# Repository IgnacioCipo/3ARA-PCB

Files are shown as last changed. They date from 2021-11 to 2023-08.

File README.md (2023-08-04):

# 3ARA-PCB

# Introduction
This repo holds the electronic boards of the project designed using KiCad.

# Images







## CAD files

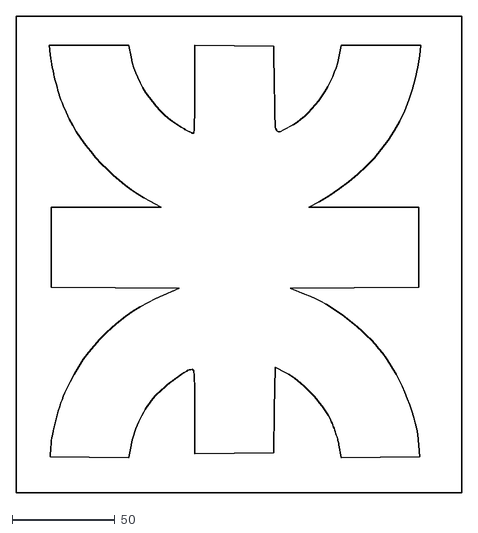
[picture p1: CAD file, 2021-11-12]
3ARA_PCB/logo_utn_kicad.dxf
217.0 x 232.0

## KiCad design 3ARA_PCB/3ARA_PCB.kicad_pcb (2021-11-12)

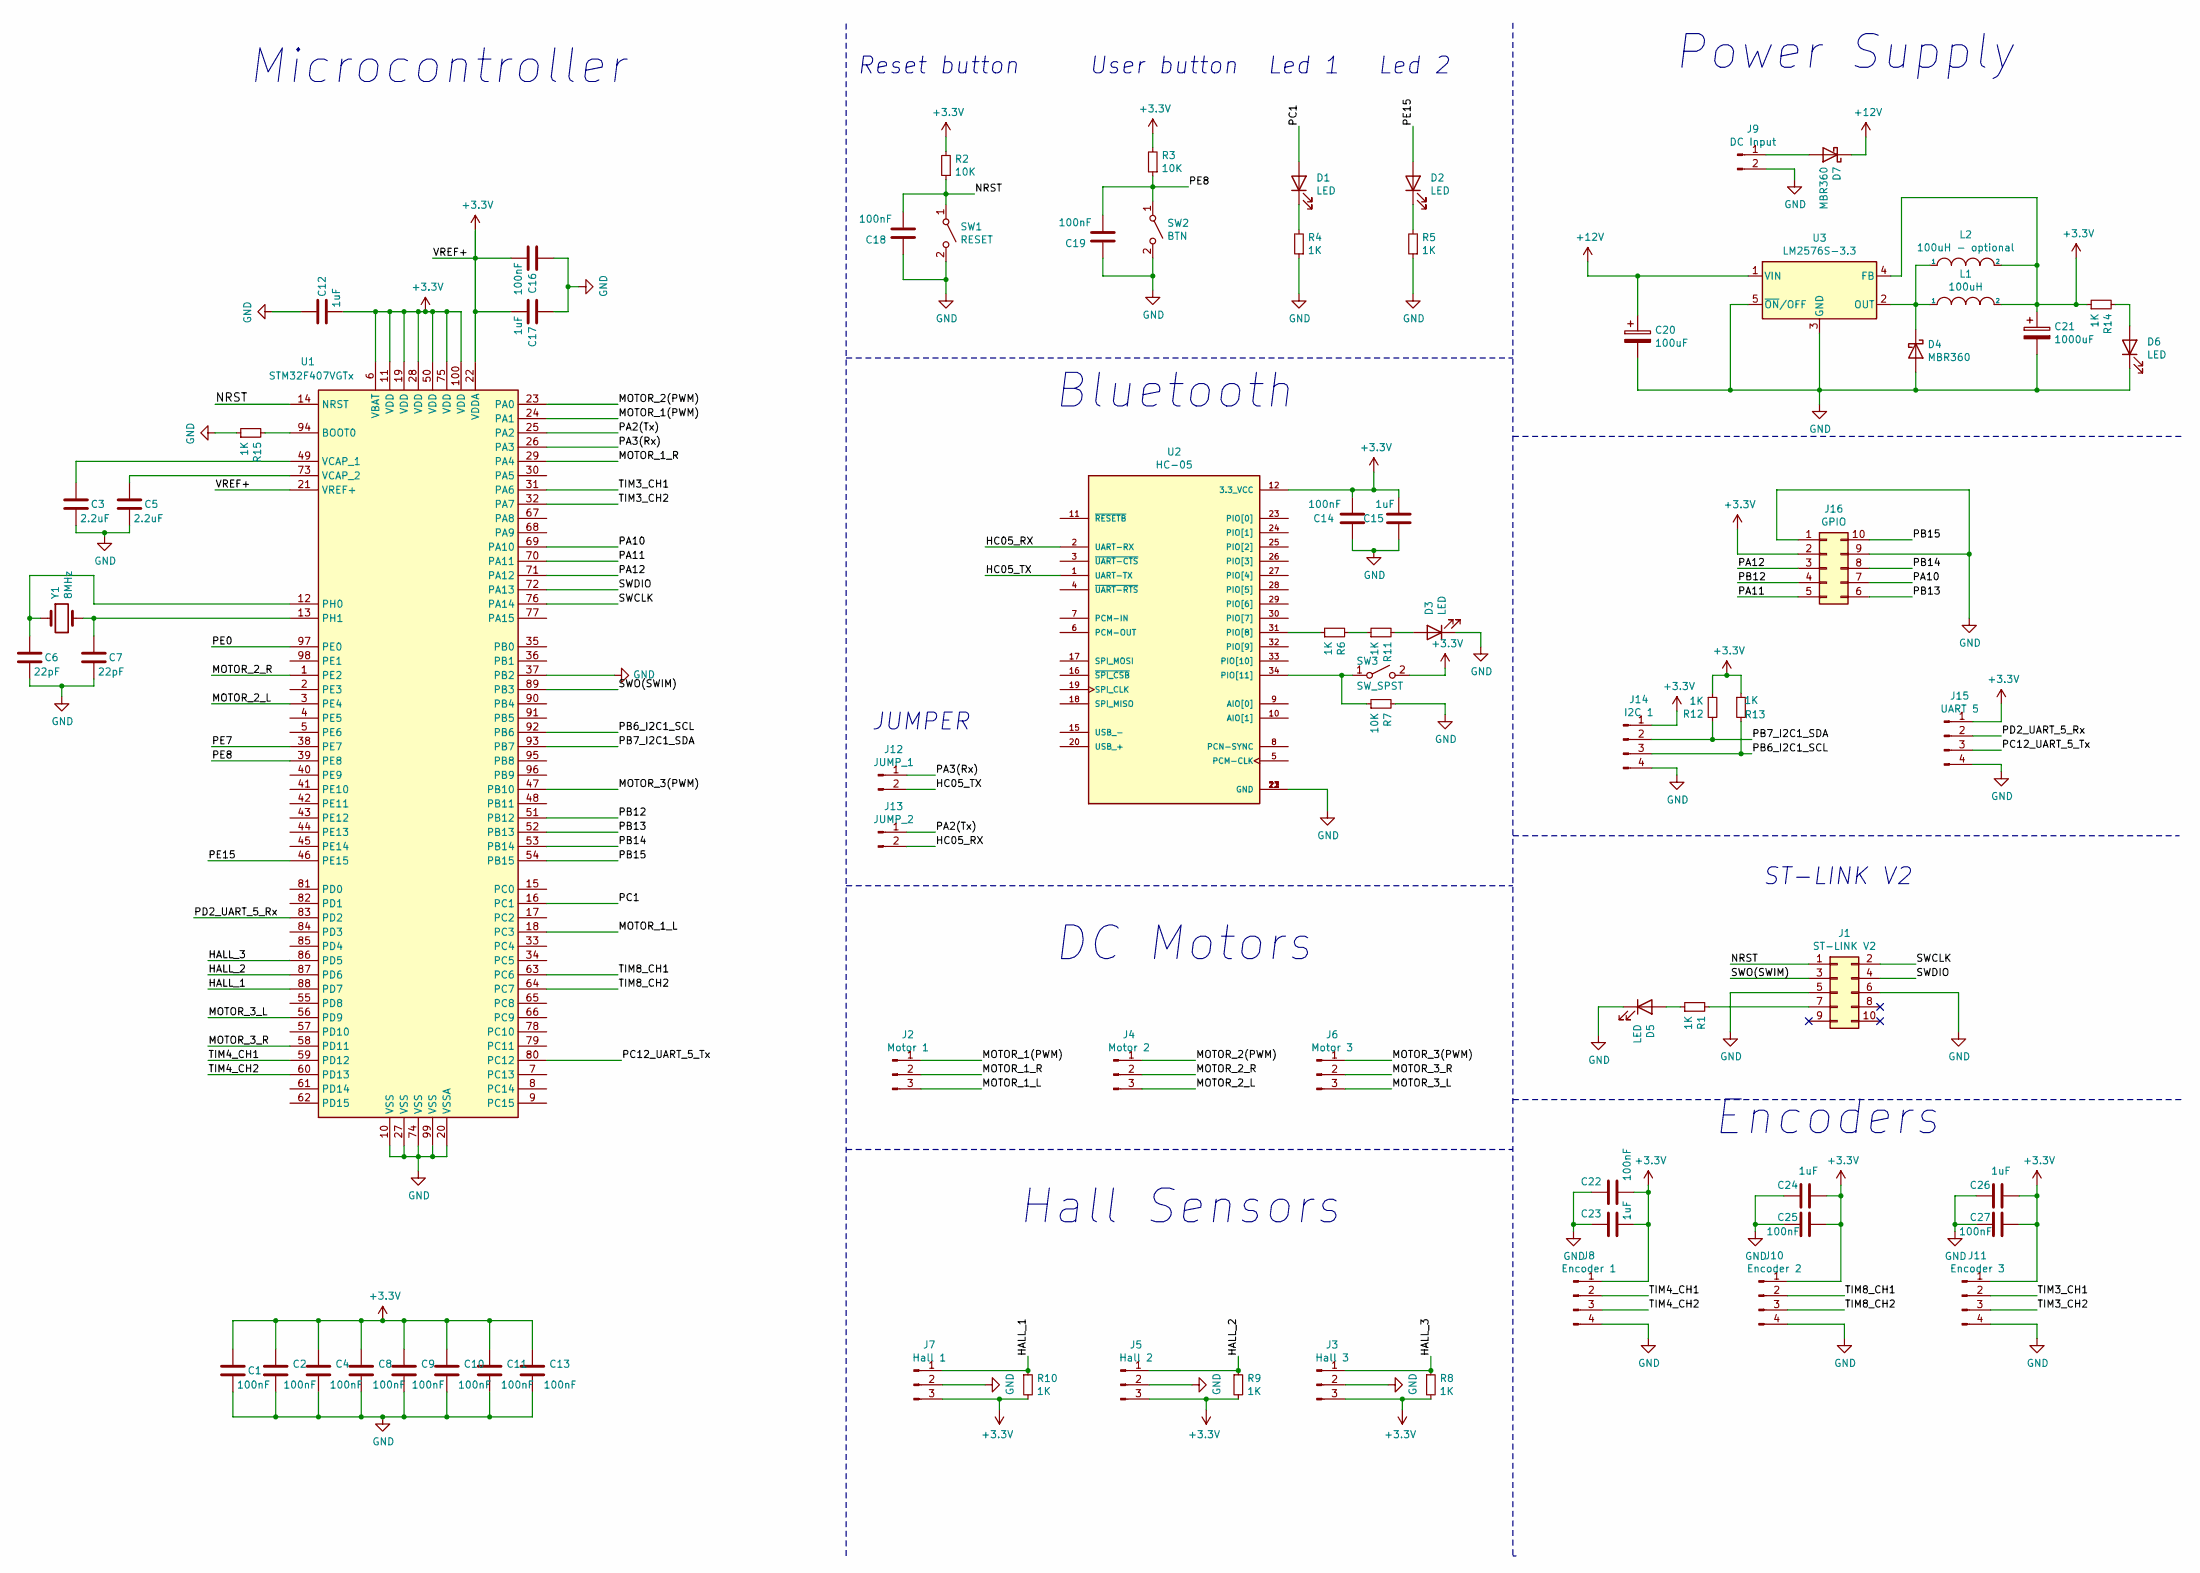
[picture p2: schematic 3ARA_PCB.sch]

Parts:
C1, C2, C4, C8, C9, C10, C11, C13, C14, C16, C18, C19, C22, C25, C27: 100nF; C_0805_2012Metric_Pad1.18x1.45mm_HandSolder
C3, C5: 2.2uF; C_Disc_D3.8mm_W2.6mm_P2.50mm
C6, C7: 22pF; C_0805_2012Metric_Pad1.18x1.45mm_HandSolder
C12, C15, C17, C23, C24, C26: 1uF; C_0805_2012Metric_Pad1.18x1.45mm_HandSolder
C20: 100uF; CP_Elec_6.3x5.4
C21: 1000uF; CP_Radial_D8.0mm_P3.50mm
D1, D6: LED; LED_1206_3216Metric_Pad1.42x1.75mm_HandSolder
D2, D3, D5: LED; LED_0805_2012Metric_Pad1.15x1.40mm_HandSolder
D4, D7: MBR360; D_SMA_Handsoldering
J1: ST-LINK V2; IDC-Header_2x05_P2.54mm_Vertical
J2: Motor 1; JST_EH_B3B-EH-A_1x03_P2.50mm_Vertical
J3: Hall 3; JST_EH_B3B-EH-A_1x03_P2.50mm_Vertical
J4: Motor 2; JST_EH_B3B-EH-A_1x03_P2.50mm_Vertical
J5: Hall 2; JST_EH_B3B-EH-A_1x03_P2.50mm_Vertical
J6: Motor 3; JST_EH_B3B-EH-A_1x03_P2.50mm_Vertical
J7: Hall 1; JST_EH_B3B-EH-A_1x03_P2.50mm_Vertical
J8: Encoder 1; JST_EH_B4B-EH-A_1x04_P2.50mm_Vertical
J9: DC Input; JST_EH_B2B-EH-A_1x02_P2.50mm_Vertical
J10: Encoder 2; JST_EH_B4B-EH-A_1x04_P2.50mm_Vertical
J11: Encoder 3; JST_EH_B4B-EH-A_1x04_P2.50mm_Vertical
J12: JUMP_1; PinHeader_1x02_P2.54mm_Vertical
J13: JUMP_2; PinHeader_1x02_P2.54mm_Vertical
J14: I2C 1; JST_EH_B4B-EH-A_1x04_P2.50mm_Vertical
J15: UART 5; JST_EH_B4B-EH-A_1x04_P2.50mm_Vertical
J16: GPIO; PinHeader_2x05_P2.54mm_Vertical
L1: 100uH; L_12x12mm_H6mm
L2: 100uH - optional; L_Axial_L9.5mm_D4.0mm_P15.24mm_Horizontal_Fastron_SMCC
R1, R4, R5, R6, R8, R9, R10, R11, R12, R13, R14, R15: 1K; R_0805_2012Metric_Pad1.20x1.40mm_HandSolder
R2, R3, R7: 10K; R_0805_2012Metric_Pad1.20x1.40mm_HandSolder
SW1: RESET; SW_PUSH_6mm
SW2: BTN; SW_PUSH_6mm
SW3: SW_SPST; SW_PUSH_6mm
U1: STM32F407VGTx; LQFP-100_14x14mm_P0.5mm
U2: HC-05; XCVR_HC-05; PARTREV v1.0
U3: LM2576S-3.3; TO-263-5_TabPin3
Y1: 8MHz; Crystal_HC49-U_Vertical

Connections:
+3V3: C1.1, C2.1, C4.1, C8.1, C9.1, C10.1, C11.1, C12.2, C13.1, C14.2, C15.2, C16.2, C17.2, C21.1, C22.2, C23.2, C24.1, C25.1, C26.1, C27.1, J3.3, J5.3, J7.3, J8.1, J10.1, J11.1, J14.1, J15.1, J16.2, L1.2, L2.2, R2.2, R3.2, R8.2, R9.2, R10.2, R12.1, R13.1, R14.1, SW3.2 (B), U1.6 (VBAT), U1.11 (VDD), U1.19 (VDD), U1.21 (VREF+), U1.22 (VDDA), U1.28 (VDD), U1.50 (VDD), U1.75 (VDD), U1.100 (VDD), U2.12 (3.3_VCC), U3.4 (FB)
+12V: C20.1, D7.1 (K), U3.1 (VIN)
/HALL_1: J7.1, R10.1, U1.88 (PD7)
/HALL_2: J5.1, R9.1, U1.87 (PD6)
/HALL_3: J3.1, R8.1, U1.86 (PD5)
/HC05_RX: J13.2, U2.2 (UART-RX)
/HC05_TX: J12.2, U2.1 (UART-TX)
/MOTOR_1(PWM): J2.1, U1.24 (PA1)
/MOTOR_1_L: J2.3, U1.18 (PC3)
/MOTOR_1_R: J2.2, U1.29 (PA4)
/MOTOR_2(PWM): J4.1, U1.23 (PA0)
/MOTOR_2_L: J4.3, U1.3 (PE4)
/MOTOR_2_R: J4.2, U1.1 (PE2)
/MOTOR_3(PWM): J6.1, U1.47 (PB10)
/MOTOR_3_L: J6.3, U1.56 (PD9)
/MOTOR_3_R: J6.2, U1.58 (PD11)
/NRST: C18.2, J1.1, R2.1, SW1.1 (A), U1.14 (NRST)
/PA2(Tx): J13.1, U1.25 (PA2)
/PA3(Rx): J12.1, U1.26 (PA3)
/PA10: J16.7, U1.69 (PA10)
/PA11: J16.5, U1.70 (PA11)
/PA12: J16.3, U1.71 (PA12)
/PB6_I2C1_SCL: J14.3, R13.2, U1.92 (PB6)
/PB7_I2C1_SDA: J14.2, R12.2, U1.93 (PB7)
/PB12: J16.4, U1.51 (PB12)
/PB13: J16.6, U1.52 (PB13)
/PB14: J16.8, U1.53 (PB14)
/PB15: J16.10, U1.54 (PB15)
/PC1: D1.2 (A), U1.16 (PC1)
/PC12_UART_5_Tx: J15.3, U1.80 (PC12)
/PD2_UART_5_Rx: J15.2, U1.83 (PD2)
/PE8: C19.2, R3.1, SW2.1 (A), U1.39 (PE8)
/PE15: D2.2 (A), U1.46 (PE15)
/SWCLK: J1.2, U1.76 (PA14)
/SWDIO: J1.4, U1.72 (PA13)
/SWO(SWIM): J1.3, U1.89 (PB3)
/TIM3_CH1: J11.2, U1.31 (PA6)
/TIM3_CH2: J11.3, U1.32 (PA7)
/TIM4_CH1: J8.2, U1.59 (PD12)
/TIM4_CH2: J8.3, U1.60 (PD13)
/TIM8_CH1: J10.2, U1.63 (PC6)
/TIM8_CH2: J10.3, U1.64 (PC7)
GND: C1.2, C2.2, C3.2, C4.2, C5.2, C6.2, C7.2, C8.2, C9.2, C10.2, C11.2, C12.1, C13.2, C14.1, C15.1, C16.1, C17.1, C18.1, C19.1, C20.2, C21.2, C22.1, C23.1, C24.2, C25.2, C26.2, C27.2, D3.1 (K), D4.2 (A), D5.1 (K), D6.1 (K), J1.5, J1.6, J3.2, J5.2, J7.2, J8.4, J9.2, J10.4, J11.4, J14.4, J15.4, J16.1, J16.9, R4.1, R5.1, R7.2, R15.1, SW1.2 (B), SW2.2 (B), U1.10 (VSS), U1.20 (VSSA), U1.27 (VSS), U1.37 (PB2), U1.74 (VSS), U1.99 (VSS), U2.13 (GND), U2.21 (GND), U2.22 (GND), U3.3 (GND), U3.5 (~ON~/OFF)
unnamed: C3.1, U1.49 (VCAP_1)
unnamed: C5.1, U1.73 (VCAP_2)
unnamed: C6.1, U1.12 (PH0), Y1.1
unnamed: C7.1, U1.13 (PH1), Y1.2
unnamed: D1.1 (K), R4.2
unnamed: D2.1 (K), R5.2
unnamed: D3.2 (A), R11.2
unnamed: D4.1 (K), L1.1, L2.1, U3.2 (OUT)
unnamed: D5.2 (A), R1.1
unnamed: D6.2 (A), R14.2
unnamed: D7.2 (A), J9.1
unnamed: J1.7, R1.2
unnamed: R6.1, U2.31 (PIO[8])
unnamed: R7.1, SW3.1 (A), U2.34 (PIO[11])
unnamed: R6.2, R11.1
unnamed: R15.2, U1.94 (BOOT0)

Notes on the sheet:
Microcontroller
Reset button
Led 1
Led 2
User button
ST-LINK V2
Bluetooth
DC Motors
Hall Sensors
Encoders
Power Supply
JUMPER

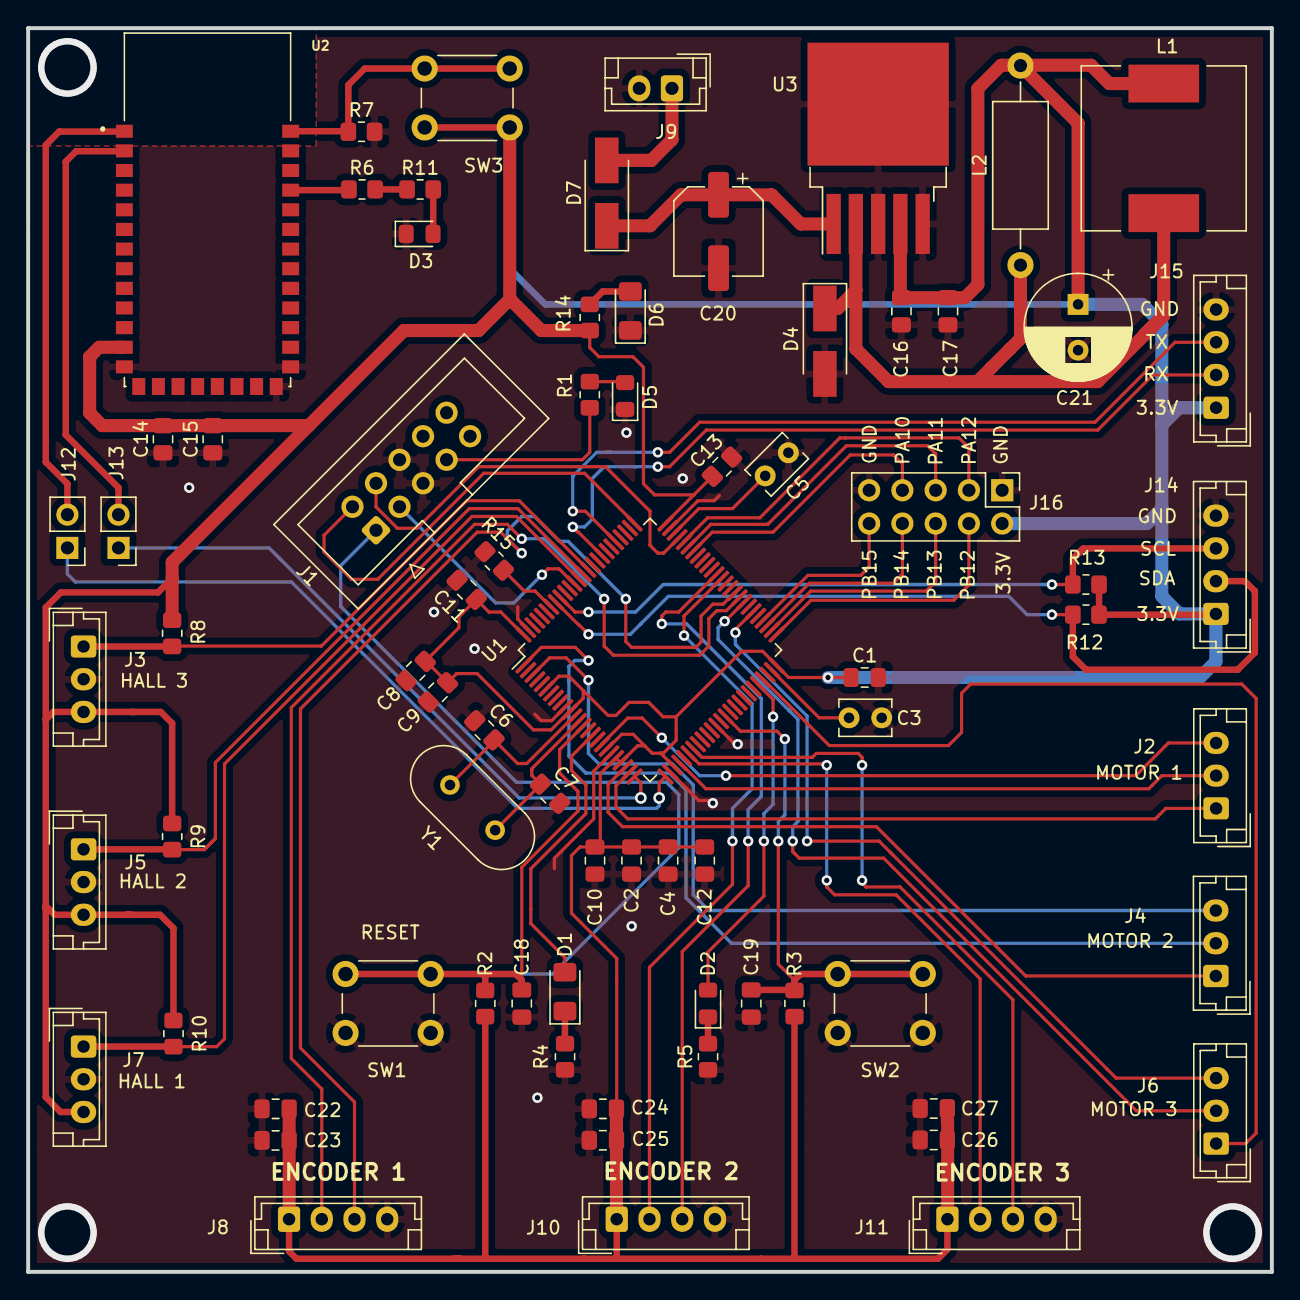
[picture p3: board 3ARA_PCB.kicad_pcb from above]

Board: 2 copper layers, 95.0 x 95.0 mm, 74 parts (0 on the bottom side), 59 nets.

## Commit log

2021-09-02 Project creation and schematic started
    [3ARA_PCB.kicad_pcb, 3ARA_PCB.sch]
2021-09-15 Continuacion del esquematico
    [3ARA_PCB.sch]
2021-09-24 Avance con el PCB
    [3ARA_PCB.kicad_pcb, 3ARA_PCB.sch]
2021-09-27 Agregado de gpios a pines
    [3ARA_PCB.kicad_pcb, 3ARA_PCB.sch]
2021-09-30 Generación de la BOM
    [3ARA_PCB.kicad_pcb, 3ARA_PCB.sch]
2021-09-30 Agregado de R pull down a boot 0 y capacitores en alimentacion
    [3ARA_PCB.kicad_pcb, 3ARA_PCB.sch]
2021-11-12 Agregado de diseño 3D para HC05
    [3ARA_PCB-B_Cu.gbr, 3ARA_PCB-B_Mask.gbr, 3ARA_PCB-B_Paste.gbr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]
2021-11-12 Agregado de diseño 3D para inductor SMD 100uH
    [3ARA_PCB.kicad_pcb]
